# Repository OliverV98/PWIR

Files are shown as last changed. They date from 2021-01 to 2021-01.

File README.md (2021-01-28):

# PWIR

## PINOUT ON STM32CUBEIDE

You can find out more information in PCB schematics or from mainboard V2.ioc

```bash
PF1 - GPIO-I ENC3A - Encoder Motor 3 encoder A
PA0 - GPIO-I ENC2_A - Encoder Motor 2 encoder A
PA2 - GPIO-I ENC1A - Encoder Motor 1 encoder A
PA3 - GPIO-I ENC1B - Encoder Motor 1 encoder B
PA4 - GPIO-I ENC3B - Encoder Motor 3 encoder B
PA5 - GPIO-O ESCPWM 
PA15 - GPIO-O SERVOPWM
PA6 - M1-PWM1 - Mootor 1 PWM1
PA7 - M1-PWM2 - Mootor 1 PWM2
PA8 - M2-PWM1 - Mootor 2 PWM1
PA9 - M2-PWM2 - Mootor 2 PWM2
PB6 - M3-PWM1 - Mootor 3 PWM1
PB7 - M3-PWM2 - Mootor 3 PWM2
PA11 - USB_DM
PA12 - USB_DP
PA13 - SWDIO
PA14 - SWCLK
```

## Functionality of motor drivers

```bash
You get information about the postion of the motor only from one encoder. That is done via GPIO-I(look pinout above). That that is used in the mainboard code to calculate PID and set the motor speed accordingly. Motor drivers get their initial PWM from mainboard that are digitally isolated(really intersting how its done).
```

## Functionality of mainboard
```bash
You send the information from the computer via USB and setup the mainboard using SWDIO and SWCLK. That is done using ST-LINK(ask instructors for it). Mainboard sends out sends out in total 8PWM signals (that of 6 are in pairs for motor drivers,1ESC,1 for servo). Becouse TIMERS were not set up correctly we had to use GIPO-O to generate the PWM signals neccesary for the functionality of ESC and SERVO. Also for the same reasons GIPO-I were used for encoder reading.
```
2021 DELTAX

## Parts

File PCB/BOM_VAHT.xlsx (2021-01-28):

Comment | Description | Designator | Footprint | LibRef | Quantity | Lehekülg | Farnell teko | Mouser teko
KEMET T491B105K035AT | 1uF Solid MnO2 Tantalum Electrolytic Capacitor; 35 V dc +/-10%; T491 Series | C5, C6 | PCB-rufcymyklsjsmb7phwvw-1 | CMP-adcf64c4c6c97208-1 | 2 | https://ee.farnell.com/kemet/t491b105k035at/cap-1-f-35v-10-smd/dp/1457432?CMP=GRHB-OCTOPART | 1457432
Panasonic EEU-FM1E471L | Capacitor; Aluminum Electrolytic; Cap 470uF; Tol 20%; Vol-Rtg 25 VDC; Radial | C9, C18, C21 | Capacitor | CMP-6b23a0732647b4e4-2 | 3 | https://ee.farnell.com/panasonic/eeufm1e471l/cap-470-f-25v-20/dp/1219470?st=panasonic%20eeu-fm1e471l | 1219470
FCI 10118192-0001LF | Conn Micro USB RCP 5 POS 0.65mm Solder RA SMD 5 Terminal 1 Port Embossed T/R | J1 | PCB-y6z8giaxv9oe4jobifng-1 | CMP-5fe6964cc67c8021-5 | 1 | https://ee.farnell.com/amphenol-icc-fci/10118192-0001lf/micro-usb-2-0-type-b-rcpt-smt/dp/2751674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 | 2751674
Bourns SRP5030T-5R6M | Inductor Power Shielded/Molded Wirewound 5.6uH 20% 100KHz Powdered Iron 4.25A 63mOhm DCR T/R | L1 | PCB-hdjvyscrw6xn5uzu8eff-1 | CMP-6d6ca5f0d7c8b2ab-1 | 1 | https://ee.farnell.com/bourns/srp5030t-5r6m/inductor-5-6uh-20-4-25a-power/dp/2309888?st=bourns%20srp5030t-5r6m | 2309888
TE Connectivity / AMP 215079-4 | Conn FFC Connector F 4 POS 1.27mm Solder ST Thru-Hole Automotive Reel | P1, P3, P4, P5, P6 | PCB-rkob87su0l0zzh8rvuwa-1 | CMP-6d83a490a6f7b244-3 | 5 | https://ee.farnell.com/amp-te-connectivity/215079-4/connector-4way-vertical-1-27/dp/1772996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 | 1772996
Samtec FTSH-105-01-L-D | CLEAR GLOVE BX 100 M - More Details | P2 | PINHEAD_2X05_127 | CMP-667845-3 | 1 | https://ee.farnell.com/samtec/ftsh-105-01-l-d/connector-header-1-27mm-pcb-10way/dp/2308436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 | 2308436
ON Semiconductor FDD6685 | MOSFET Transistor, P Channel, -40 A, -30 V, 0.014 ohm, -10 V, -1.8 V | Q1 | INF-PG-TO252-3-11_M | CMP-1302df0e83a1ccc5-2 | 1 | https://ee.farnell.com/on-semiconductor/fdd6685/mosfet-p-smd-to-252/dp/1471043?st=on%20semiconductor%20fdd6685 | 1471043
LM2937IMP-5.0/NOPB | 500 mA Low Dropout Regulator, 4-pin SOT-223, Pb-Free | U1 | MP04A_L | CMP-0062-01757-3 | 1 | https://ee.farnell.com/texas-instruments/lm2937imp-5-0-nopb/ldo-0-5vdo-5v-0-5a-3sot223/dp/3122066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 | 3122066
STMicroelectronics USBLC6-2SC6 | USBLC6 Series 2 Line 6 V Uni / Bi-Directional ESD Protection - SOT-23-6 | U2 | SOT95P280X145-6N | CMP-756ebe39126caaa9-8 | 1 | https://ee.farnell.com/stmicroelectronics/usblc6-2sc6/esd-protection-3-5pf-17v-sot23/dp/1269406RL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 | 1269406RL
Texas Instruments ISO7760DWR | High Speed, Robust EMC Six-Channel Digital Isolators 16-SOIC -55 to 125 | U3 | PCB-tizc0j283js4s37wua64-1 | CMP-7f8db395d75da04a-1 | 1 | https://www.mouser.ee/ProductDetail/Texas-Instruments/ISO7760DWR?qs=BZBei1rCqCAKosCUp1v8Jg%3D%3D |  | 595- ISO7760DWR
MCP1701AT-3302I/CB | 2 µA Low-Dropout Positive Voltage Regulator, 3-Pin SOT-23A, Industrial Temperature, Tape and Reel | U4 | SOT-23A-CB3_L | CMP-1501331-2 | 1 | https://ee.farnell.com/microchip/mcp1701at-3302i-cb/ic-ldo-reg-250ma-3-3v-sot-23a/dp/1605554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 | 1605554
STMicroelectronics STM32G431K8T6 | Mainstream Arm CORTEX-M4 Core Wi | U5 | PCB-roa9pse9auixlf5bq7cm-1 | CMP-333afc1f6528ecfd-2 | 1 | https://ee.farnell.com/stmicroelectronics/stm32g431k8t6/mcu-32bit-170mhz-lqfp-32/dp/3515807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 | 3515807
Texas Instruments DRV8874PWPR | 38-V, 6-A H-bridge motor driver with integrated current sensing & feedback 16-HTSSOP -40 to 125 | U6, U7, U8 | PCB-45171vetpwtrcknlr443-1 | CMP-1fd4d0c2f6c9c013-7 | 3 | https://www.mouser.ee/ProductDetail/Texas-Instruments/DRV8874PWPR |  | 595-DRV8874PWPR
SI8620BB-B-IS | General Purpose tal Isolator 2500Vrms 2 Channel 150Mbps 35kV/µs CMTI 8-SOIC (0.154 , 3.90mm Width) | U9 | PCB-426hnsna86ae4ms1a3g5-1 | CMP-11cfd913bf49ce08-1 | 1 | https://ee.farnell.com/silicon-labs/si8620bb-b-is/digital-isolator-8ns-nsoic-8/dp/2423240?CMP=GRHB-OCTOPART | 2423240
Texas Instruments TPS56339DDCR | 4.5-V to 24-V input, 3-A output synchronous buck converter 6-SOT-23-THIN -40 to 125 | U10 | PCB-gq8lm18lv5jhlhr4rj8l-1 | CMP-bcda73dcd896631d-3 | 1 | https://www.mouser.ee/ProductDetail/Texas-Instruments/TPS56339DDCR |  | 595-TPS56339DDCR
teko = | tellimiskood

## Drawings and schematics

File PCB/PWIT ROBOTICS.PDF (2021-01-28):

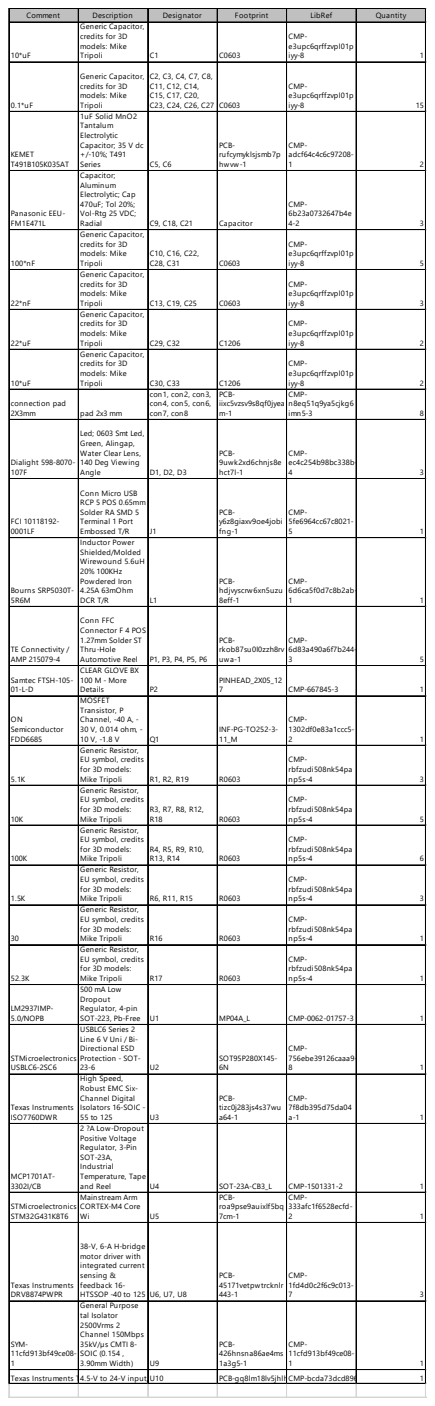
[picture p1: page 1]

Comment | Description | Designator | Footprint | LibRef | Quantity
10*uF | Generic Capacitor, credits for 3D models: Mike Tripoli | C1 | C0603 | CMP-e3upc6qrffzvpl01p iyy-8 | 1

0.1*uF | Generic Capacitor, credits for 3D models: Mike Tripoli | C2, C3, C4, C7, C8, C11, C12, C14, C15, C17, C20, C23, C24, C26, C27 | C0603 | CMP-e3upc6qrffzvpl01p iyy-8 | 15

KEMET T491B105K035AT | 1uF Solid MnO2 Tantalum Electrolytic Capacitor; 35 V dc +/-10%; T491 Series | C5, C6 | PCB-rufcymyklsjsmb7p hwvw-1 | CMP-adcf64c4c6c97208-1 | 2

Panasonic EEU-FM1E471L | Capacitor; Aluminum Electrolytic; Cap 470uF; Tol 20%; Vol-Rtg 25 VDC; Radial | C9, C18, C21 | Capacitor | CMP-6b23a0732647b4e 4-2 | 3

100*nF | Generic Capacitor, credits for 3D models: Mike Tripoli | C10, C16, C22, C28, C31 | C0603 | CMP-e3upc6qrffzvpl01p iyy-8 | 5

22*nF | Generic Capacitor, credits for 3D models: Mike Tripoli | C13, C19, C25 | C0603 | CMP-e3upc6qrffzvpl01p iyy-8 | 3

22*uF | Generic Capacitor, credits for 3D models: Mike Tripoli | C29, C32 | C1206 | CMP-e3upc6qrffzvpl01p iyy-8 | 2

10*uF | Generic Capacitor, credits for 3D models: Mike Tripoli | C30, C33 | C1206 | CMP-e3upc6qrffzvpl01p iyy-8 | 2

connection pad 2X3mm | pad 2x3 mm | con1, con2, con3, con4, con5, con6, con7, con8 | PCB-iixc5vzsv9s8qf0jyea m-1 | CMP-n8eq51q9ya5cjkg6 imn5-3 | 8

Dialight 598-8070-107F | Led; 0603 Smt Led, Green, Alingap, Water Clear Lens, 140 Deg Viewing Angle | D1, D2, D3 | PCB-9uwk2xd6chnjs8e hct7l-1 | CMP-ec4c254b98bc338b-4 | 3

FCI 10118192-0001LF | Conn Micro USB RCP 5 POS 0.65mm Solder RA SMD 5 Terminal 1 Port Embossed T/R | J1 | PCB-y6z8giaxv9oe4jobi fng-1 | CMP-5fe6964cc67c8021-5 | 1

Bourns SRP5030T-5R6M | Inductor Power Shielded/Molded Wirewound 5.6uH 20% 100KHz Powdered Iron 4.25A 63mOhm DCR T/R | L1 | PCB-hdjvyscrw6xn5uzu 8eff-1 | CMP-6d6ca5f0d7c8b2ab-1 | 1

TE Connectivity / AMP 215079-4 | Conn FFC Connector F 4 POS 1.27mm Solder ST Thru-Hole Automotive Reel | P1, P3, P4, P5, P6 | PCB-rkob87su0l0zzh8rv uwa-1 | CMP-6d83a490a6f7b244-3 | 5

Samtec FTSH-105-01-L-D | CLEAR GLOVE BX 100 M - More Details | P2 | PINHEAD_2X05_12 7 | CMP-667845-3 | 1

ON Semiconductor FDD6685 | MOSFET Transistor, P Channel, -40 A, -30 V, 0.014 ohm, -10 V, -1.8 V | Q1 | INF-PG-TO252-3-11_M | CMP-1302df0e83a1ccc5-2 | 1

5.1K | Generic Resistor, EU symbol, credits for 3D models: Mike Tripoli | R1, R2, R19 | R0603 | CMP-rbfzudi508nk54pa np5s-4 | 3

10K | Generic Resistor, EU symbol, credits for 3D models: Mike Tripoli | R3, R7, R8, R12, R18 | R0603 | CMP-rbfzudi508nk54pa np5s-4 | 5

100K | Generic Resistor, EU symbol, credits for 3D models: Mike Tripoli | R4, R5, R9, R10, R13, R14 | R0603 | CMP-rbfzudi508nk54pa np5s-4 | 6

1.5K | Generic Resistor, EU symbol, credits for 3D models: Mike Tripoli | R6, R11, R15 | R0603 | CMP-rbfzudi508nk54pa np5s-4 | 3

30 | Generic Resistor, EU symbol, credits for 3D models: Mike Tripoli | R16 | R0603 | CMP-rbfzudi508nk54pa np5s-4 | 1

52.3K | Generic Resistor, EU symbol, credits for 3D models: Mike Tripoli | R17 | R0603 | CMP-rbfzudi508nk54pa np5s-4 | 1

LM2937IMP-5.0/NOPB | 500 mA Low Dropout Regulator, 4-pin SOT-223, Pb-Free | U1 | MP04A_L | CMP-0062-01757-3 | 1

STMicroelectronics USBLC6-2SC6 | USBLC6 Series 2 Line 6 V Uni / Bi-Directional ESD Protection - SOT-23-6 | U2 | SOT95P280X145-6N | CMP-756ebe39126caaa9-8 | 1

Texas Instruments ISO7760DWR | High Speed, Robust EMC Six-Channel Digital Isolators 16-SOIC -55 to 125 | U3 | PCB-tizc0j283js4s37wu a64-1 | CMP-7f8db395d75da04 a-1 | 1

MCP1701AT-3302I/CB | 2 ?A Low-Dropout Positive Voltage Regulator, 3-Pin SOT-23A, Industrial Temperature, Tape and Reel | U4 | SOT-23A-CB3_L | CMP-1501331-2 | 1

STMicroelectronics STM32G431K8T6 | Mainstream Arm CORTEX-M4 Core Wi | U5 | PCB-roa9pse9auixlf5bq 7cm-1 | CMP-333afc1f6528ecfd-2 | 1

Texas Instruments DRV8874PWPR | 38-V, 6-A H-bridge motor driver with integrated current sensing & feedback 16-HTSSOP -40 to 125 | U6, U7, U8 | PCB-45171vetpwtrcknlr 443-1 | CMP-1fd4d0c2f6c9c013-7 | 3

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

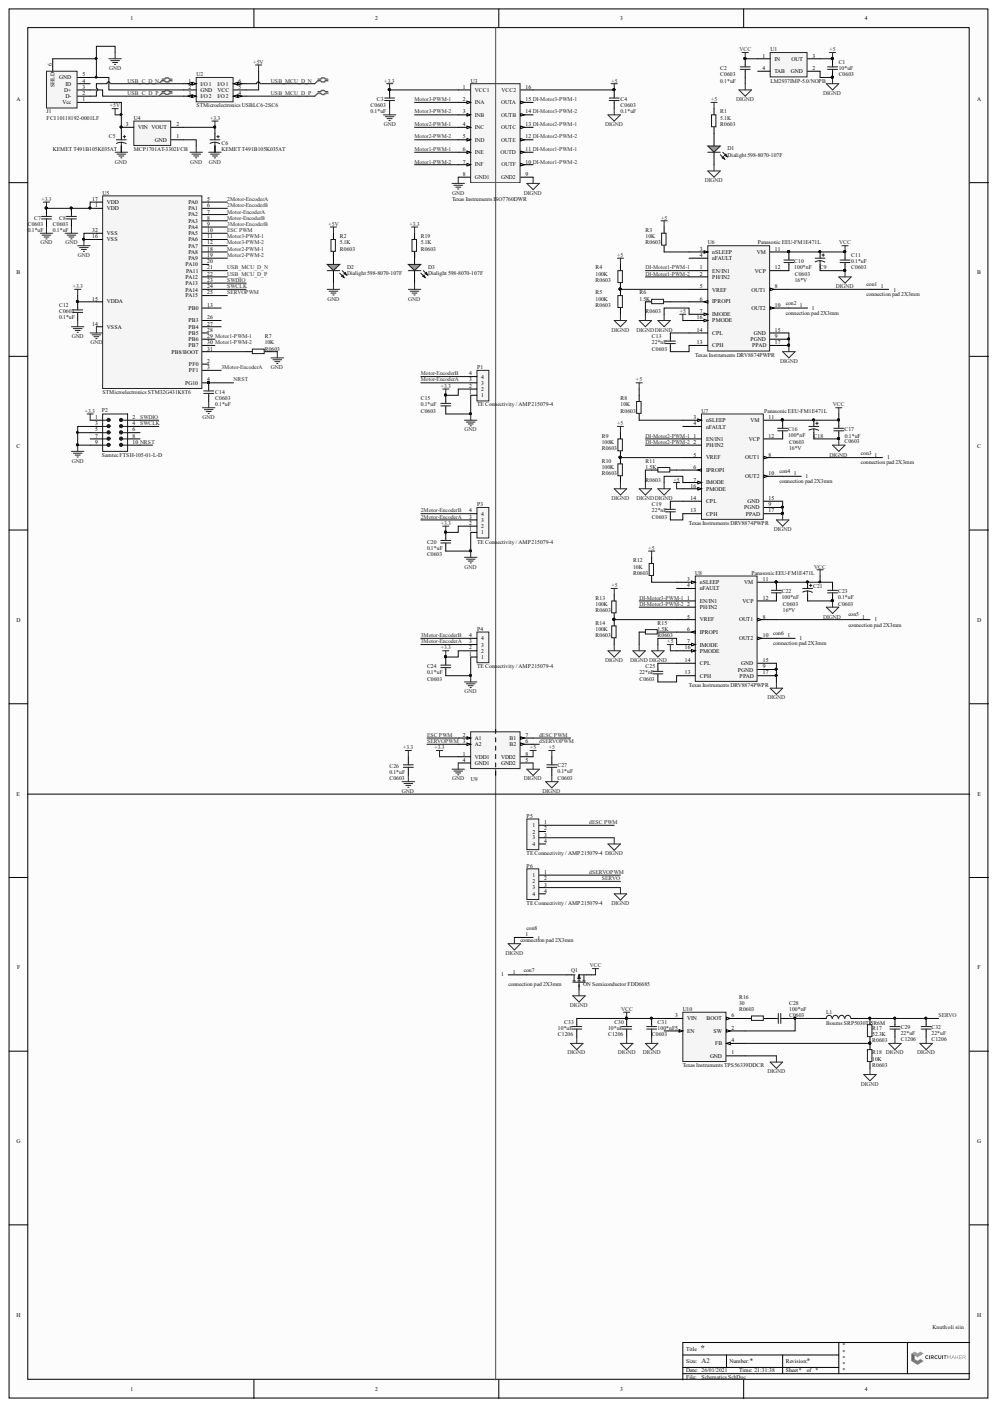
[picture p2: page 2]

VCC U1 +5 +5 R3

Title * | * * * * *

1 2 | 3 | File: Schematics.SchDoc 4

Size: A2 | Number: * | Revision: *

Date: 26/01/2021 Time: 21:31:38 | | Sheet * of *

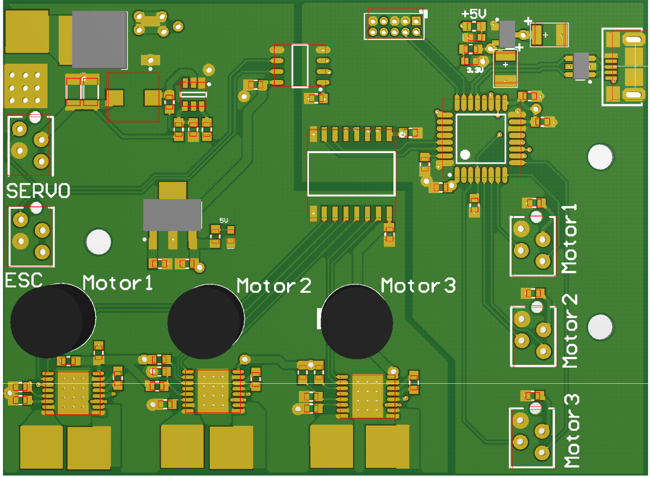
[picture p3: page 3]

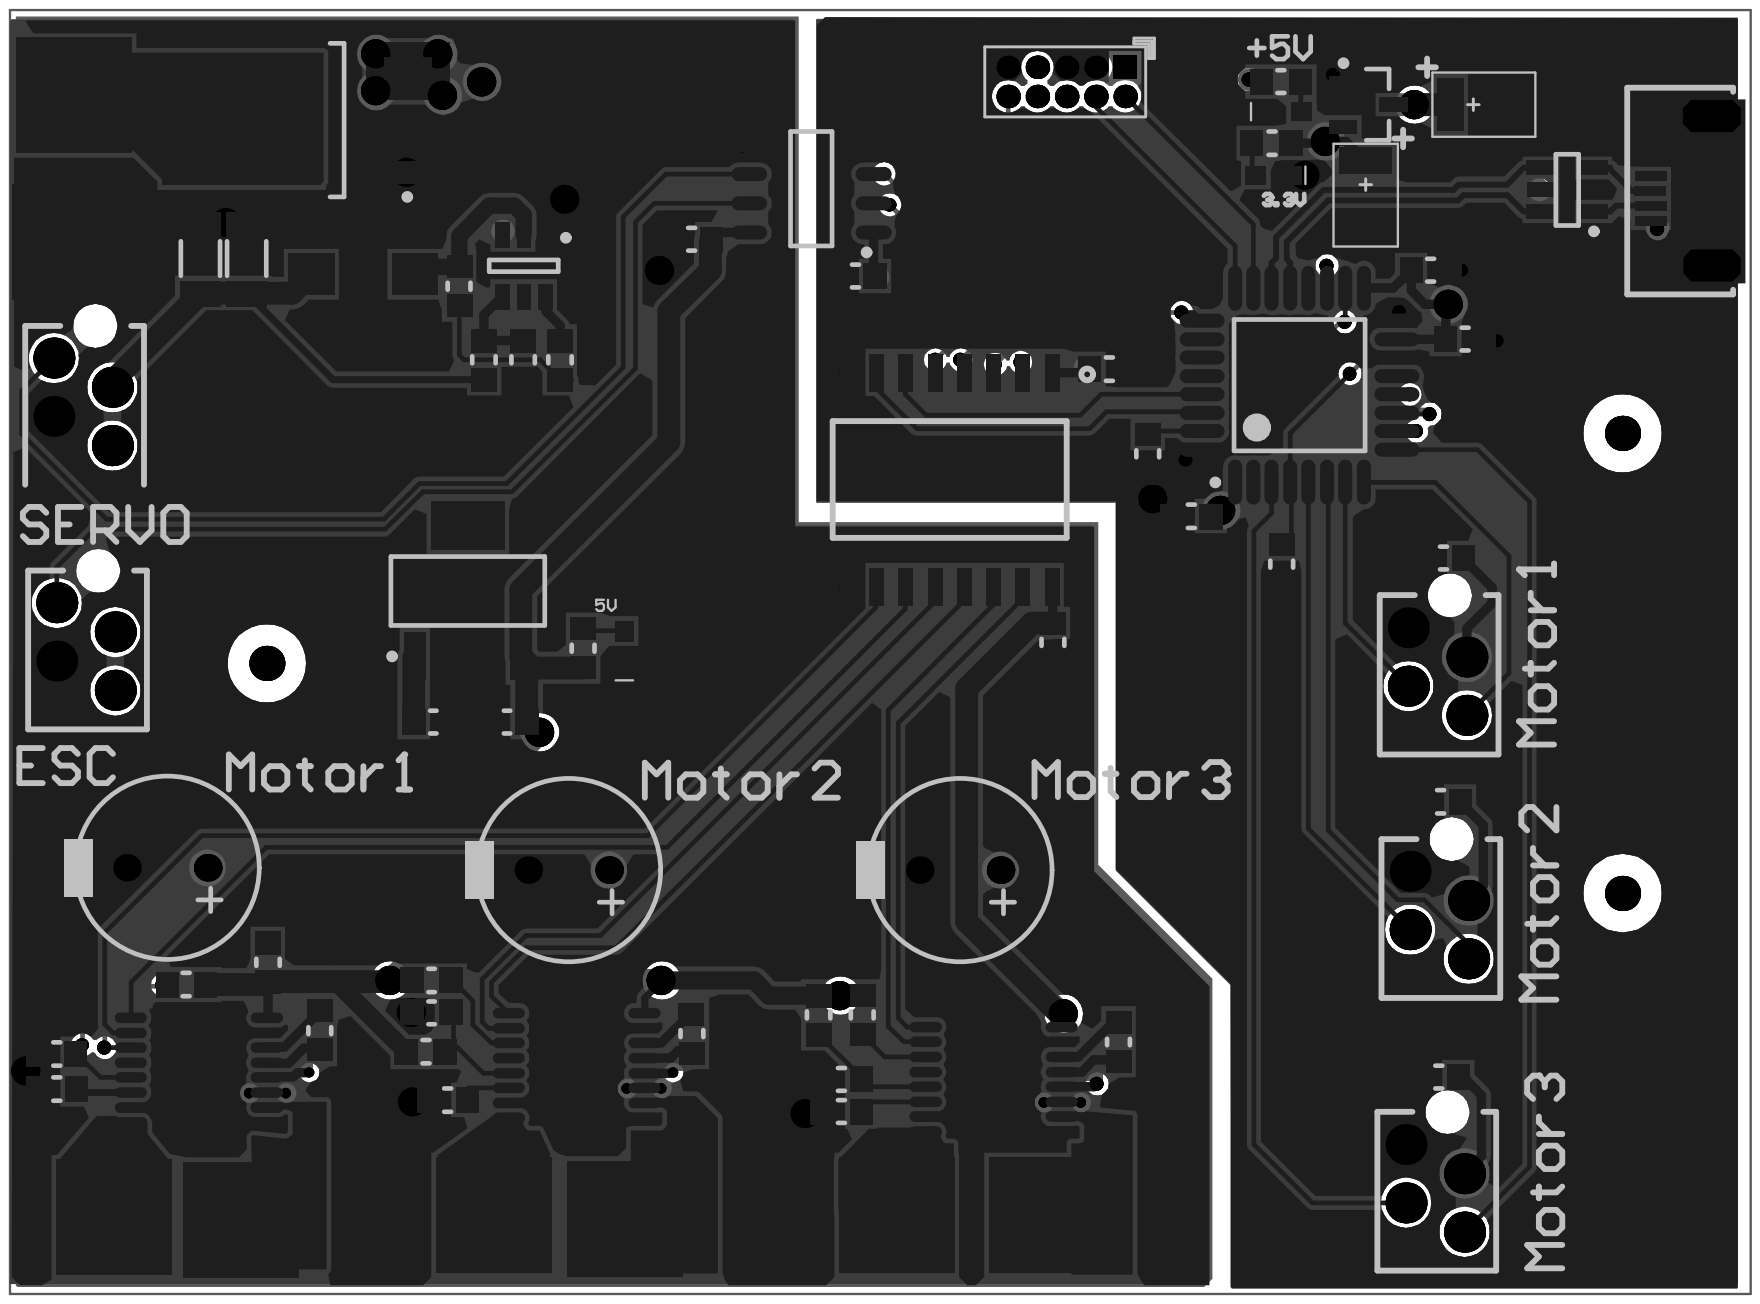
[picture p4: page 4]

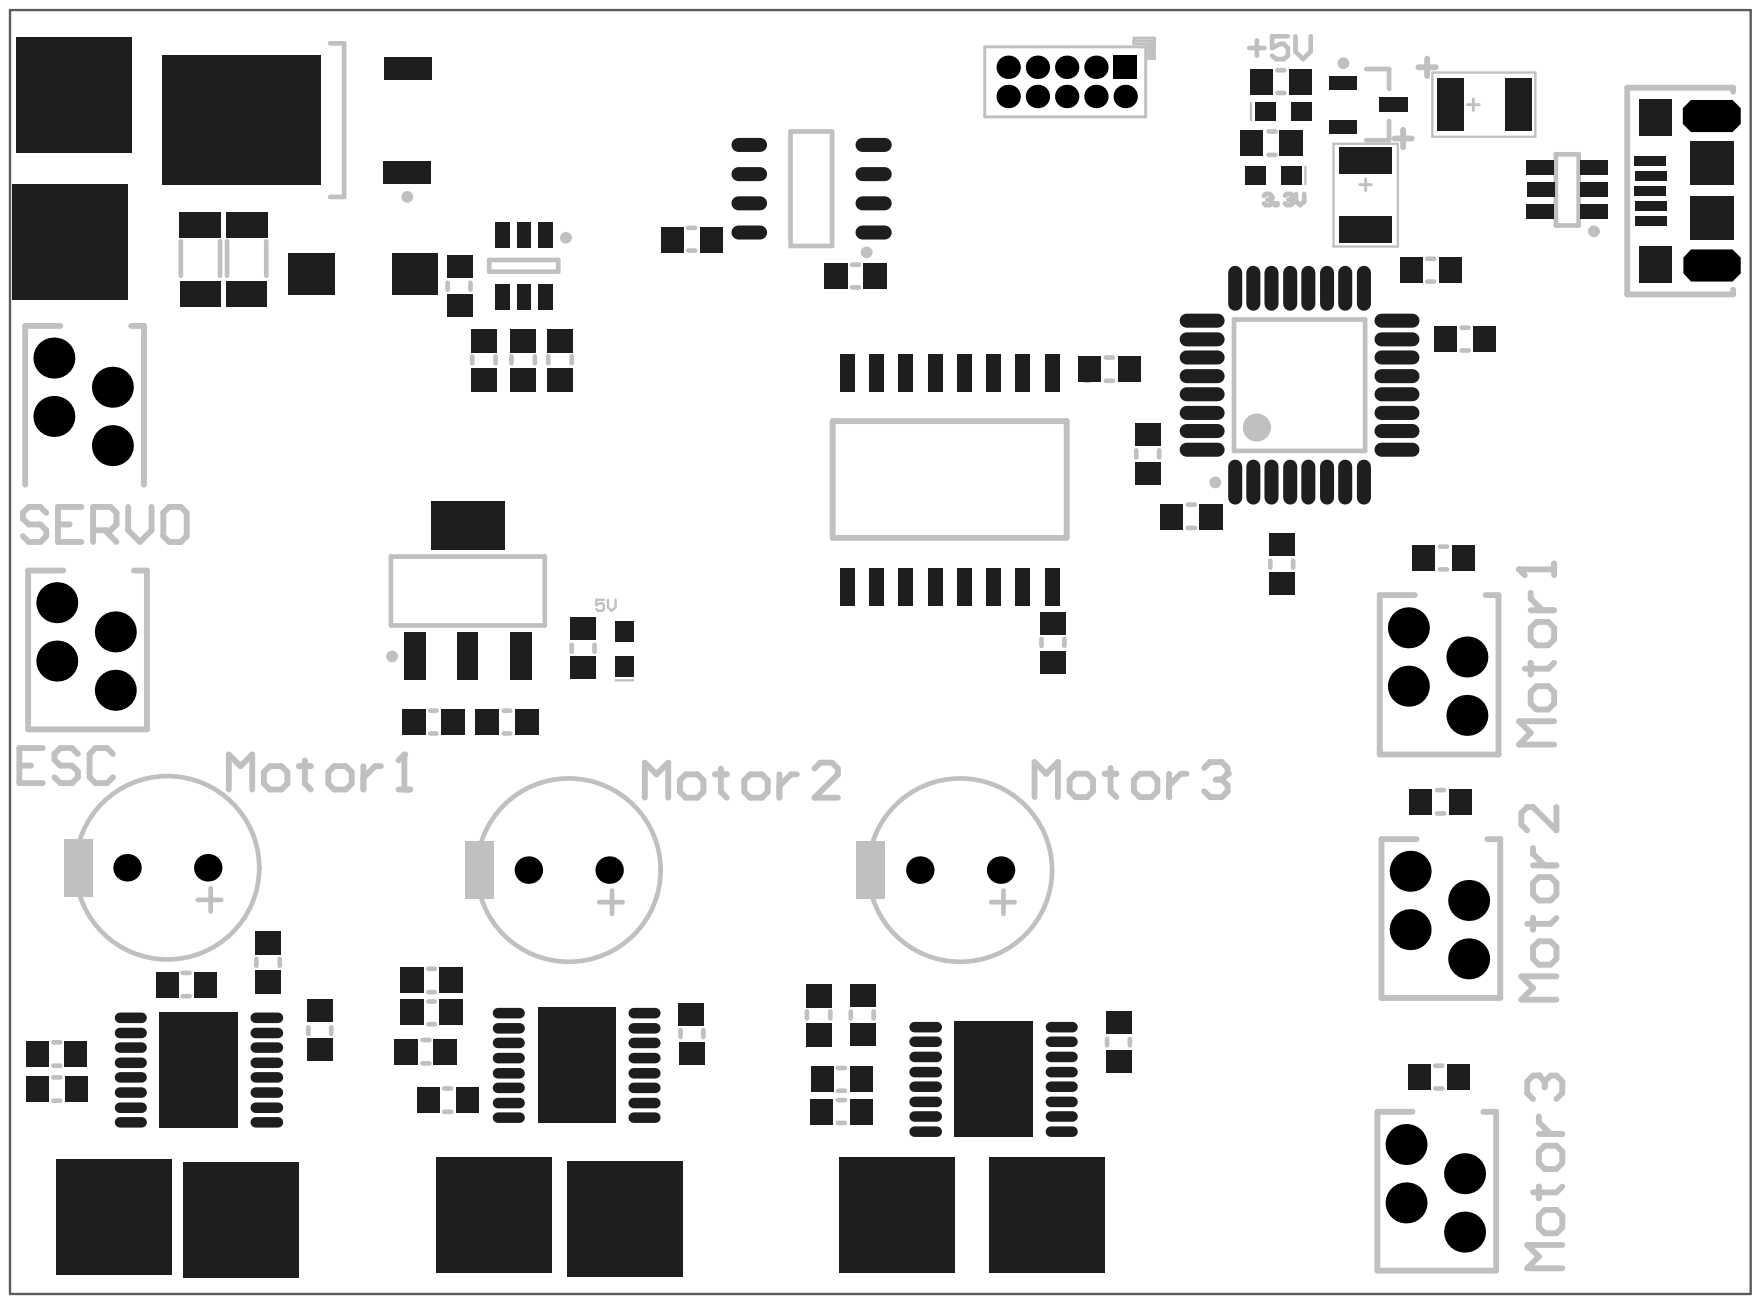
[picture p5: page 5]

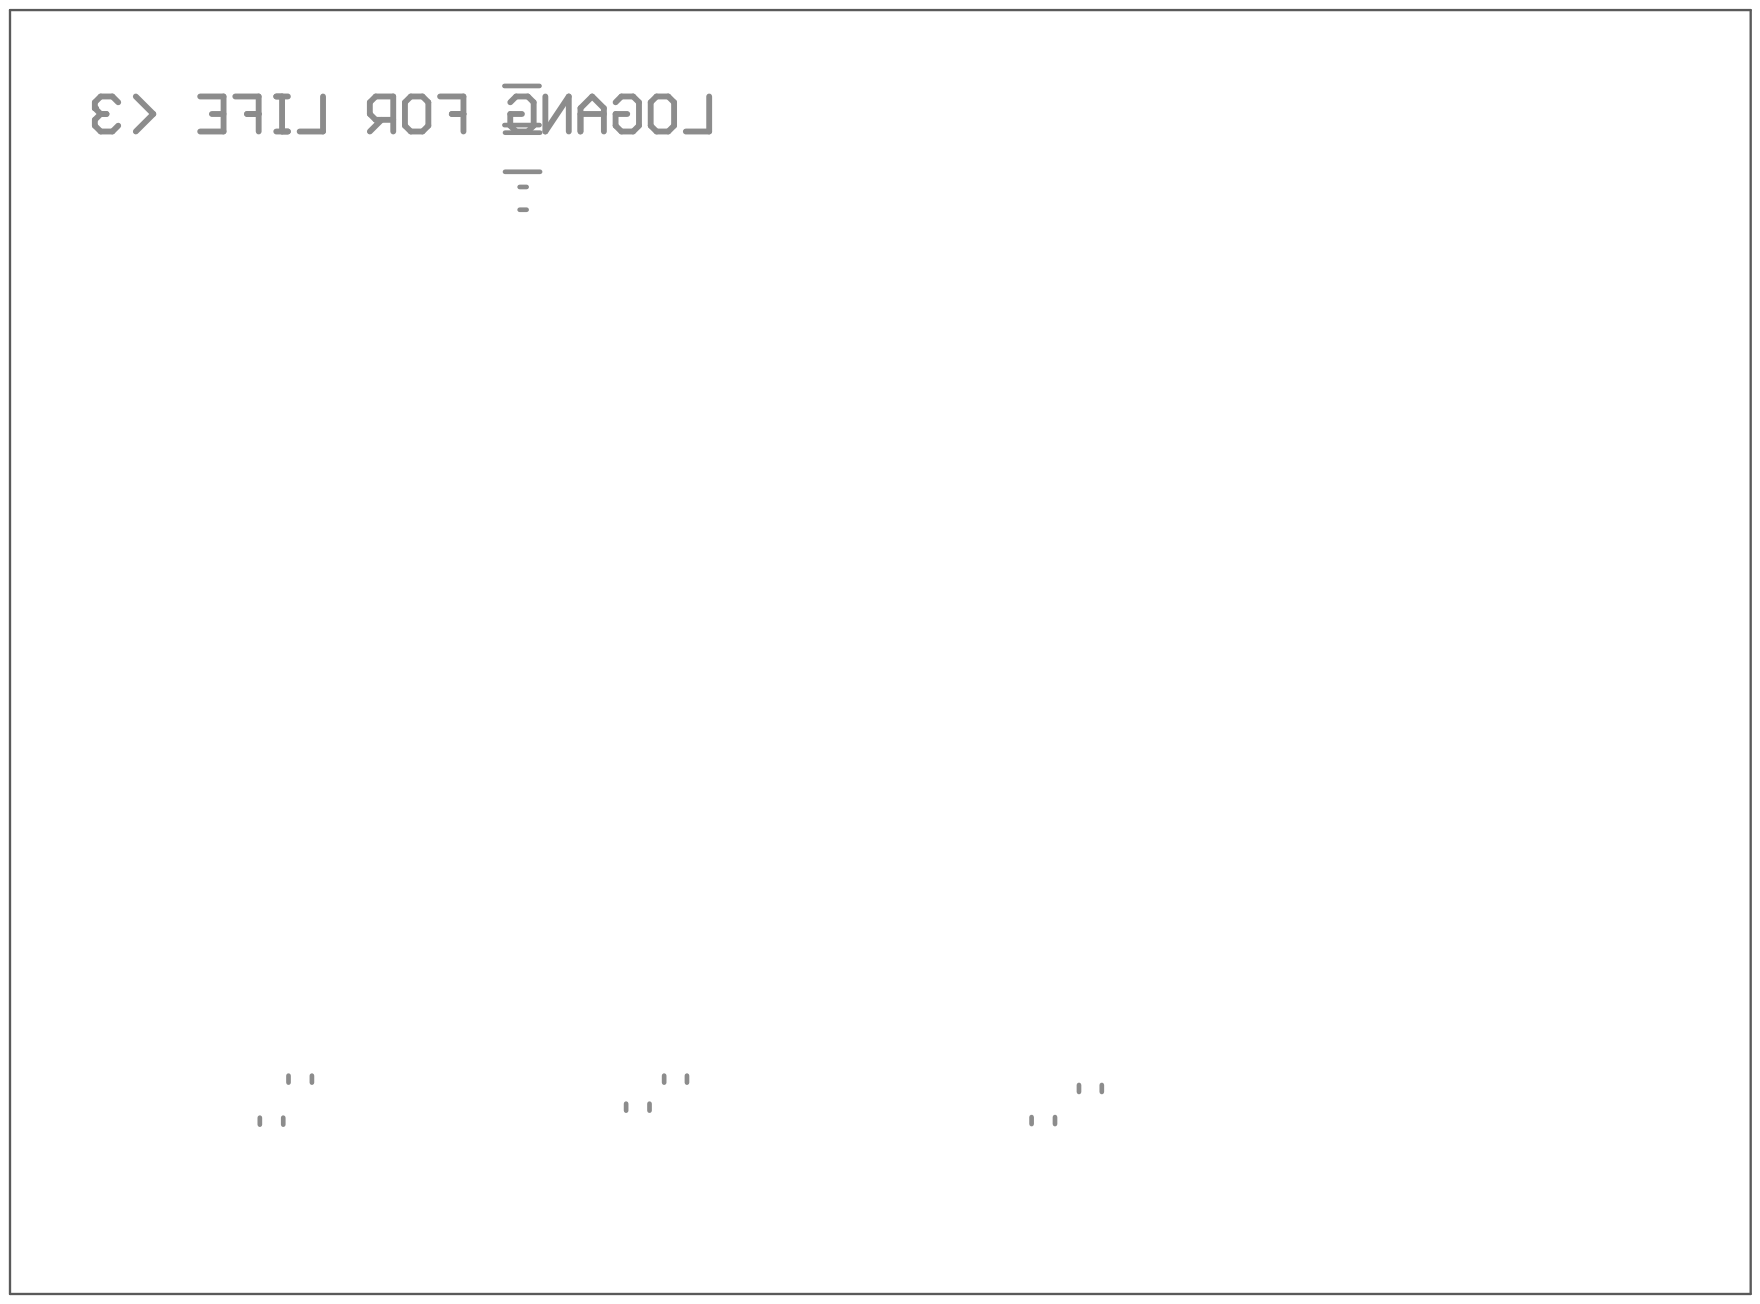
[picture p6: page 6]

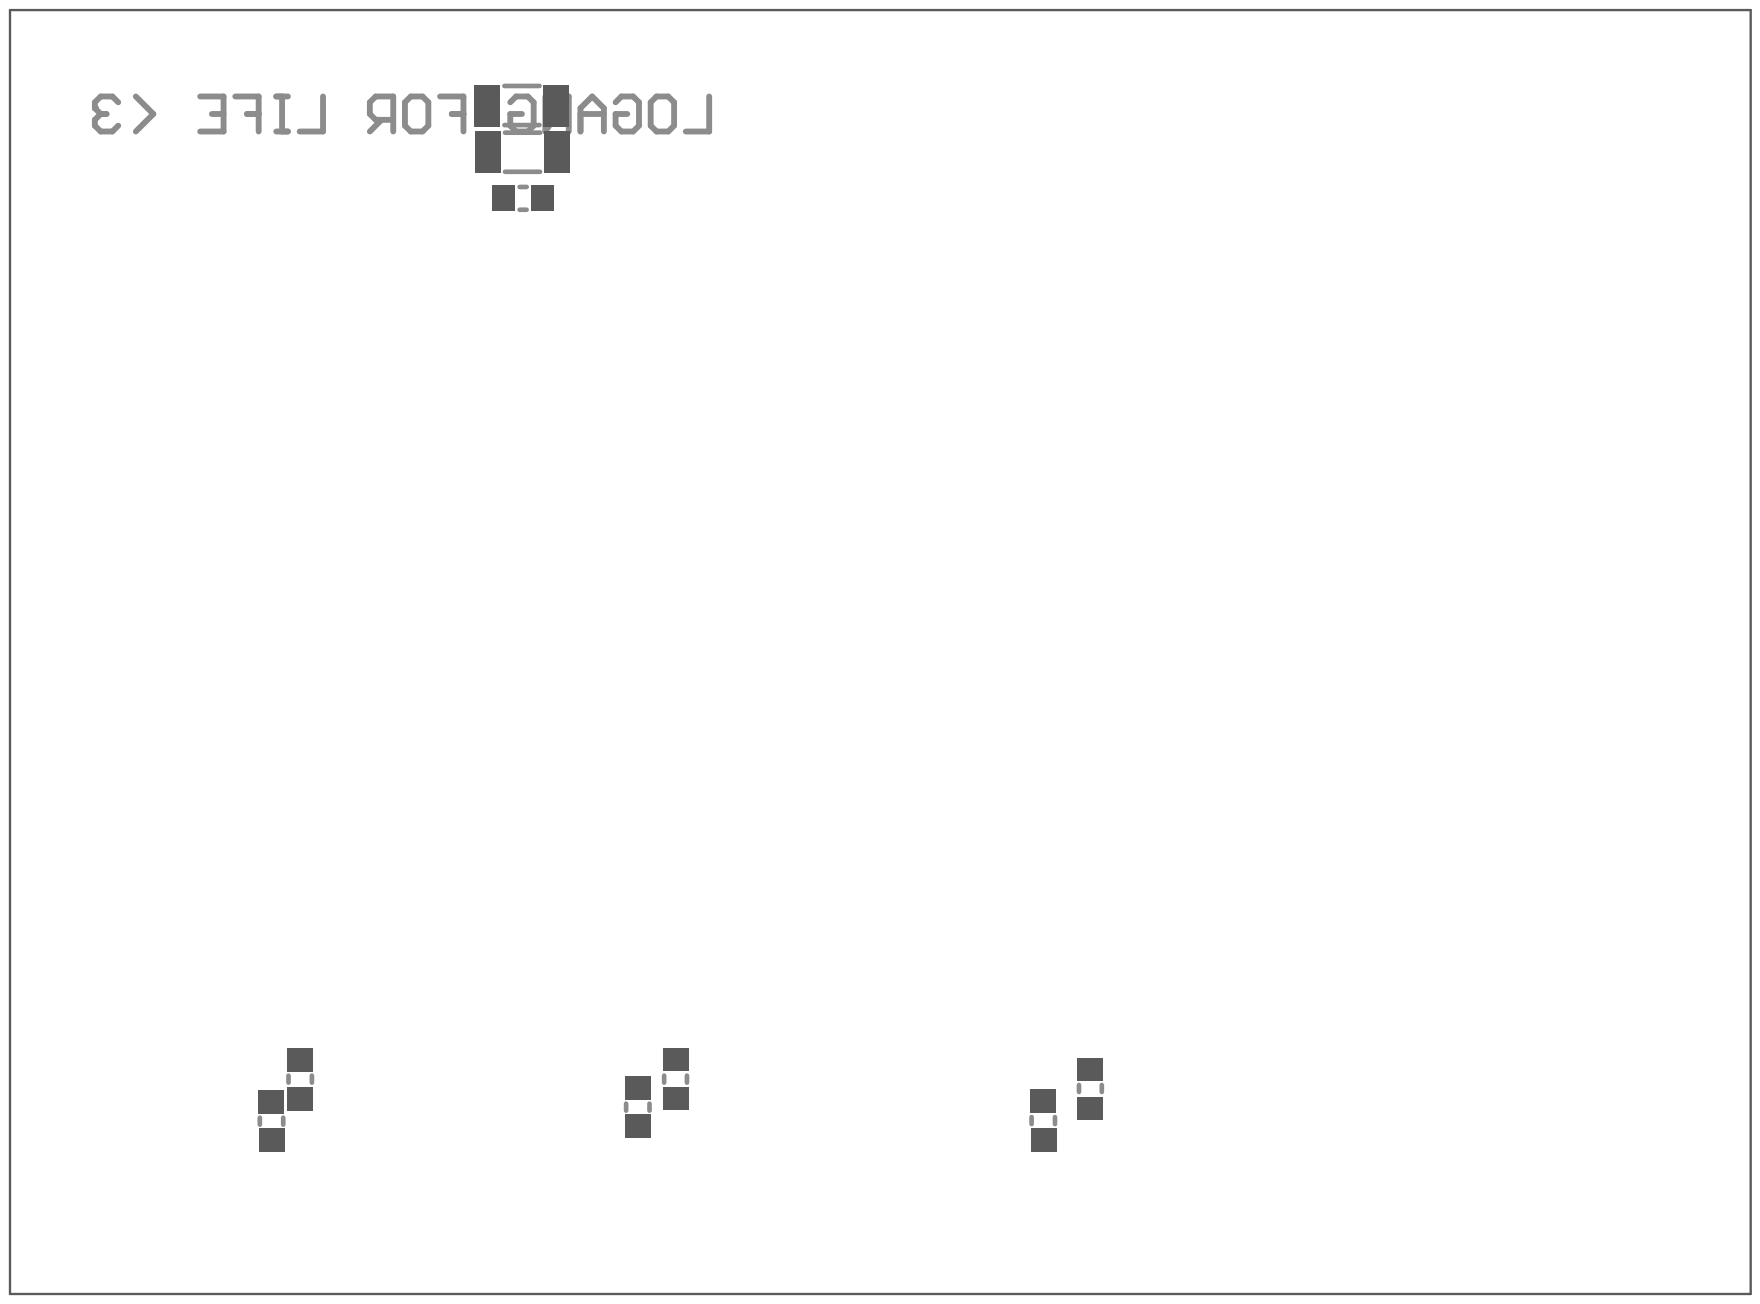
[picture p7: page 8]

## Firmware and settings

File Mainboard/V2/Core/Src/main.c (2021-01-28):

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
/* Includes ------------------------------------------------------------------*/
#include "main.h"
#include "usb_device.h"

TIM_HandleTypeDef htim1;
TIM_HandleTypeDef htim3;
TIM_HandleTypeDef htim4;
TIM_HandleTypeDef htim8;
TIM_HandleTypeDef htim16;

void SystemClock_Config(void);
static void MX_GPIO_Init(void);
static void MX_TIM1_Init(void);
static void MX_TIM3_Init(void);
static void MX_TIM4_Init(void);
static void MX_TIM8_Init(void);
static void MX_TIM16_Init(void);
/* USER CODE BEGIN 0 */
typedef struct Command { // (1)
	int8_t motor1;
	int8_t motor2;
	int8_t motor3;
	int32_t thrower;
	int32_t servo;
	int32_t ir;
//	float pGain;
//	float iGain;
//	float dGain;
	int32_t pid_type;
	uint8_t delimiter;
	int8_t speed1;
	int8_t speed2;
	int8_t speed3;
	int8_t throwerSpeed;

} Command;


Command command, feedback;
volatile uint8_t command_received = 0;
volatile uint8_t command_received_ticker = 0;

Motor motor1;
Motor motor2;
Motor motor3;


typedef struct Feedback { // (3)
  int16_t speed1;
  int16_t speed2;
  int16_t speed3;
  uint16_t delimiter;
} Feedback;

typedef struct Received{
	uint8_t speed1;
	uint8_t speed2;
	uint8_t speed3;
	uint8_t throwerSpeed;
	uint8_t servospeed;
	uint8_t delimiter;
} Received;

Received received = {.speed1 = 125, .speed2 = 125, .speed3 = 125, .throwerSpeed = 0,.servospeed = 0, .delimiter = 0}; // (4)
volatile uint8_t isCommandReceived = 0; // (5)
volatile float pGain, iGain, dGain = 0;


void CDC_On_Receive(uint8_t* buffer, uint32_t* length) {

  if (*length == sizeof(Received)) {
	  memcpy(&received, buffer, sizeof(Received));

	 if (received.delimiter == 0xAA) { // (9)
		  isCommandReceived = 1;
    }
  }
}


void Set_Motor_Speed(volatile uint32_t *channel_a, //copy paste
		volatile uint32_t *channel_b, int32_t motor_speed) {
	if (motor_speed > 0) {
		// forward
		if (motor_speed <= MOTORS_MAX_SPEED) {
			// 0 to 100 compact range
			*channel_a = motor_speed * MOTORS_CO + MOTORS_MIN_CCR;
		} else {
			// 100 to 65535 full range
			*channel_a = motor_speed;
		}
		*channel_b = 0;
	} else if (motor_speed < 0) {
		// backward
		if (motor_speed >= -MOTORS_MAX_SPEED) {
			// -100 to 0 compact range
			*channel_b = motor_speed * -MOTORS_CO + MOTORS_MIN_CCR;
		} else {
			// -65535 to -100 full range
			*channel_b = motor_speed * -1;
		}
		*channel_a = 0;
	} else {
		// stop
		*channel_a = 0;
		*channel_b = 0;
	}
}


int PID2(uint8_t enc, uint8_t setpoint){


	enc = 250 - enc;

	float P = 0.4;
	float I = 0.00001;
	float D = 0;

	static long integral = 0;

	if(setpoint == 0){
		integral = 0;
		return 0;
	}


	//CDC_Transmit_FS(&enc, sizeof(enc));

	float error = setpoint - enc;

	integral += error;

	int out = 50 + P*error + I*integral;

	if(out < 0){
		out = 0;
	}


	if(out > 100) out = 100;

	//CDC_Transmit_FS(&out, sizeof(out));
	return (uint8_t)out;
}
/* USER CODE END 0 */

/**
  * @brief  The application entry point.
  * @retval int
  */
int main(void)
{
  /* USER CODE BEGIN 1 */


    /* Initialize Rotary encoder 2, pin A = PF1, pin B = PA2 */


    /* Rotate LCD */

    /* Initialize Rotary encoder 1, pin A = PF1, pin B = PD1 */

  /* USER CODE END 1 */

  /* MCU Configuration--------------------------------------------------------*/

  /* Reset of all peripherals, Initializes the Flash interface and the Systick. */
  HAL_Init();

  /* USER CODE BEGIN Init */
  CoreDebug->DEMCR |= CoreDebug_DEMCR_TRCENA_Msk;
    DWT->CYCCNT = 0;
    DWT->CTRL |= DWT_CTRL_CYCCNTENA_Msk;

    unsigned long esctimer = DWT->CYCCNT;
    unsigned long servotimer = DWT->CYCCNT;
  /* USER CODE END Init */

  /* Configure the system clock */
  SystemClock_Config();

  /* Initialize all configured peripherals */
  MX_GPIO_Init();
  MX_TIM1_Init();
  MX_TIM3_Init();
  MX_TIM4_Init();
  MX_TIM8_Init();
  MX_TIM16_Init();
  MX_USB_Device_Init();
  /* USER CODE BEGIN 2 */
 // HAL_TIM_Encoder_Start(&htim2, TIM_CHANNEL_1 | TIM_CHANNEL_2);

    HAL_TIM_PWM_Start(&htim1, TIM_CHANNEL_1);
  	HAL_TIM_PWM_Start(&htim1, TIM_CHANNEL_2);
  	TIM1->CCR1 = 0;
  	TIM1->CCR2 = 0;


  	HAL_TIM_PWM_Start(&htim3, TIM_CHANNEL_1);
  	HAL_TIM_PWM_Start(&htim3, TIM_CHANNEL_2);
  	TIM3->CCR1 = 0;
  	TIM3->CCR2 = 0;


  	HAL_TIM_PWM_Start(&htim4, TIM_CHANNEL_1);
  	HAL_TIM_PWM_Start(&htim4, TIM_CHANNEL_2);
  	TIM4->CCR1 = 0;
  	TIM4->CCR2 = 0;


typedef struct Feedback{
	int16_t speed1;
	int16_t speed2;
	int16_t speed3;
	int16_t delmiter;
} Feedback;

  /* USER CODE END 2 */

  /* Infinite loop */
  /* USER CODE BEGIN WHILE */
	int ENC2 = 0;
	int prev_ENC2 = 0;
	unsigned long ENCA_S = DWT->CYCCNT;
	unsigned long ENCA_D;
	uint8_t ENCA_P = 0;

	unsigned long ENCA_S1 = DWT->CYCCNT;
	unsigned long ENCA_D1;
	uint8_t ENCA_P3 = 0;

	unsigned long ENCA_S3 = DWT->CYCCNT;
	unsigned long ENCA_D3;
	uint8_t ENCA_P2 = 0;
  while (1)
  {


	  //ESC
	  if((DWT->CYCCNT - esctimer)/96000 > 20){
		  esctimer = DWT->CYCCNT;
		  HAL_GPIO_WritePin(ESCPWM_GPIO_Port, ESCPWM_Pin,1);
		  while((DWT->CYCCNT - esctimer) / 96 < (received.throwerSpeed*3.92+1000));
		  HAL_GPIO_WritePin(ESCPWM_GPIO_Port, ESCPWM_Pin,0);
	  }



	  //SERVO
	  if((DWT->CYCCNT - servotimer)/96000 > 2){
		  servotimer = DWT->CYCCNT;
		  HAL_GPIO_WritePin(SERVOPWM_GPIO_Port, SERVOPWM_Pin,1);
		  while((DWT->CYCCNT - servotimer) / 96 < (received.servospeed*23));
		  HAL_GPIO_WritePin(SERVOPWM_GPIO_Port, SERVOPWM_Pin,0);
	  }







	  	  unsigned long while_timeout = DWT->CYCCNT;
	  	  int timeout_flag = 0;
		  while(HAL_GPIO_ReadPin(ENC2_A_GPIO_Port, ENC2_A_Pin) == 1){  // ootab kuni läheb madalaks
			  if((DWT->CYCCNT - while_timeout)/2000 > 249){
				  timeout_flag = 1;
				  break;
			  }
		  }
		  while_timeout = DWT->CYCCNT;
		  while(HAL_GPIO_ReadPin(ENC2_A_GPIO_Port, ENC2_A_Pin) == 0){ //ootab kuni läheb kõrgeks
			  if((DWT->CYCCNT - while_timeout)/2000 > 249){
				  timeout_flag = 1;
				  break;
			  }
		  }
		  while_timeout = DWT->CYCCNT;
		  ENCA_S = DWT->CYCCNT;
		  while(HAL_GPIO_ReadPin(ENC2_A_GPIO_Port, ENC2_A_Pin) == 1){ // ootab kuni läheb madalaks
			  if((DWT->CYCCNT - while_timeout)/2000 > 249){
				  timeout_flag = 1;
				  break;
			  }
		  }

		  ENCA_D = ((DWT->CYCCNT - ENCA_S) / 2000);
		  if(ENCA_D > 249 || timeout_flag == 1) ENCA_D = 249;
		  ENCA_P = (uint8_t)ENCA_D;





		  while_timeout = DWT->CYCCNT;
		  timeout_flag = 0;
		  while(HAL_GPIO_ReadPin(ENC1A_GPIO_Port, ENC1A_Pin) == 1){  // ootab kuni läheb madalaks
			  if((DWT->CYCCNT - while_timeout)/2000 > 249){
				  timeout_flag = 1;
				  break;
			  }
		  }
		  while_timeout = DWT->CYCCNT;
		  while(HAL_GPIO_ReadPin(ENC1A_GPIO_Port, ENC1A_Pin) == 0){ //ootab kuni läheb kõrgeks
			  if((DWT->CYCCNT - while_timeout)/2000 > 249){
				  timeout_flag = 1;
				  break;
			  }
		  }
		  while_timeout = DWT->CYCCNT;
		  ENCA_S = DWT->CYCCNT;
		  while(HAL_GPIO_ReadPin(ENC1A_GPIO_Port, ENC1A_Pin) == 1){ // ootab kuni läheb madalaks
			  if((DWT->CYCCNT - while_timeout)/2000 > 249){
				  timeout_flag = 1;
				  break;
			  }
		  }

		  ENCA_D = ((DWT->CYCCNT - ENCA_S) / 2000);
		  if(ENCA_D > 249 || timeout_flag == 1) ENCA_D = 249;
		  ENCA_P3 = (uint8_t)ENCA_D;







		  while_timeout = DWT->CYCCNT;
  	  	  timeout_flag = 0;
  		  while(HAL_GPIO_ReadPin(ENC3A_GPIO_Port, ENC3A_Pin) == 1){  // ootab kuni läheb madalaks
  			  if((DWT->CYCCNT - while_timeout)/2000 > 249){
  				  timeout_flag = 1;
  				  break;
  			  }
  		  }
  		  while_timeout = DWT->CYCCNT;
  		  while(HAL_GPIO_ReadPin(ENC3A_GPIO_Port, ENC3A_Pin) == 0){ //ootab kuni läheb kõrgeks
  			  if((DWT->CYCCNT - while_timeout)/2000 > 249){
  				  timeout_flag = 1;
  				  break;
  			  }
  		  }
  		  while_timeout = DWT->CYCCNT;
  		  ENCA_S = DWT->CYCCNT;
  		  while(HAL_GPIO_ReadPin(ENC3A_GPIO_Port, ENC3A_Pin) == 1){ // ootab kuni läheb madalaks
  			  if((DWT->CYCCNT - while_timeout)/2000 > 249){
  				  timeout_flag = 1;
  				  break;
  			  }
  		  }

		  ENCA_D = ((DWT->CYCCNT - ENCA_S) / 2000);
		  if(ENCA_D > 249 || timeout_flag == 1) ENCA_D = 249;
		  ENCA_P2 = (uint8_t)ENCA_D;






		if(received.speed1 > 125){
			uint8_t pi1d = PID2(ENCA_P3, (received.speed1 - 125)*2);
			Set_Motor_Speed(&(TIM4->CCR1), &(TIM4->CCR2), pi1d);
		}
		else if(received.speed1 < 125){
			uint8_t pi1d = PID2(ENCA_P3, 250 - (received.speed1*2));
			Set_Motor_Speed(&(TIM4->CCR1), &(TIM4->CCR2), pi1d*-1);
		}
		else{
			Set_Motor_Speed(&(TIM4->CCR1), &(TIM4->CCR2), 0);
		}



		if(received.speed2 > 125){
			uint8_t pi2d = PID2(ENCA_P, (received.speed2 - 125)*2);
			Set_Motor_Speed(&(TIM1->CCR1), &(TIM1->CCR2), pi2d);
		}
		else if(received.speed2 < 125){
			uint8_t pi2d = PID2(ENCA_P, 250 - (received.speed2*2));
			Set_Motor_Speed(&(TIM1->CCR1), &(TIM1->CCR2), pi2d*-1);
		}
		else{
			Set_Motor_Speed(&(TIM1->CCR1), &(TIM1->CCR2), 0);
		}





		if(received.speed3 > 125){
			uint8_t pi3d = PID2(ENCA_P2, (received.speed3 - 125)*2);
			Set_Motor_Speed(&(TIM3->CCR1), &(TIM3->CCR2), pi3d);
		}
		else if(received.speed3 < 125){
			uint8_t pi3d = PID2(ENCA_P2, 250 - (received.speed3*2));
			Set_Motor_Speed(&(TIM3->CCR1), &(TIM3->CCR2), pi3d*-1);
		}
		else{
			Set_Motor_Speed(&(TIM3->CCR1), &(TIM3->CCR2), 0);
		}






	    //CDC_Transmit_FS(&ENCA_P, sizeof(ENCA_P));



	//	uint8_t pi3d = PID2(ENCA_P3, received.speed3);
	//  CDC_Transmit_FS(&pid, sizeof(pid));
	// 	Set_Motor_Speed(&(TIM4->CCR1), &(TIM4->CCR2), pi3d);


    /* USER CODE END WHILE */

    /* USER CODE BEGIN 3 */
  }
  /* USER CODE END 3 */
}

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
/* USER CODE BEGIN 4 */
void HAL_TIM_PeriodElapsedCallback(TIM_HandleTypeDef *htim) {
//	unsigned long t1 = DWT->CYCCNT;

	//Handle_Encoder(&motor1, TIM2->CNT);
	//Handle_Encoder(&motor2, TIM2->CNT);

	//Handle_Encoder(&motor3, TIM4->CNT);
	if (command.pid_type == 0) {
	//	feedback.motor1 = motor1.cur_enc_speed;
		//received.speed2 = motor2.cur_enc_speed;

		//feedback.motor3 = motor3.cur_enc_speed;
	} else {
	//	feedback.motor1 = motor1.enc_speed_hist_avg;
		//received.speed2 = motor2.enc_speed_hist_avg;
	//	feedback.motor3 = motor3.enc_speed_hist_avg;
	}

	//Calculate_PID(&motor1);
//	Calculate_PID(&motor2);
	//Calculate_PID(&motor3);
	//Set_Motor_Speed(&(TIM1->CCR1), &(TIM1->CCR2), motor1.cur_speed);//motor1.cur_speed
	//Set_Motor_Speed(&(TIM3->CCR1), &(TIM3->CCR2), motor2.cur_speed);
	//Set_Motor_Speed(&(TIM4->CCR1), &(TIM4->CCR2), motor3.cur_speed);

	// servo stopper
//	if (HAL_GPIO_ReadPin(GPIOB, GPIO_PIN_3) && !command.ir) {
//		TIM17->CCR1 = 0;
//s	}

	// timeout
	if (command_received_ticker > 0) {
		command_received_ticker -= 1;
	} else {
		// stop wheels
		TIM1->CCR1 = 0;
		TIM1->CCR2 = 0;
		TIM3->CCR1 = 0;
		TIM3->CCR2 = 0;
		TIM4->CCR1 = 0;
		TIM4->CCR2 = 0;


	}
//	unsigned long t2 = DWT->CYCCNT;
//	unsigned long diff = t2 - t1;
}

/* USER CODE END 4 */
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


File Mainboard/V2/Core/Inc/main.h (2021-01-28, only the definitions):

#define MOTORS_MIN_CCR 20000
#define MOTORS_MAX_CCR 65000
#define MOTORS_MAX_SPEED 100
#define MOTORS_CO ((MOTORS_MAX_CCR - MOTORS_MIN_CCR) / MOTORS_MAX_SPEED)
#define ESC_IDLE_CCR 4000
#define ESC_MIN_CCR 4200
#define ESC_MAX_CCR 7000
#define ESC_MAX_SPEED 100
#define ESC_CO ((ESC_MAX_CCR - ESC_MIN_CCR) / ESC_MAX_SPEED)
#define SERVO_IN_MIN_CCR 4700
#define SERVO_OUT_MIN_CCR 5000
#define SERVO_MAX_SPEED 100
#define SERVO_CO (400/SERVO_MAX_SPEED)
#define ENCODER_MAX 65535
#define ENCODER_QUADRANT (ENCODER_MAX / 4)
#define ENCODER_QUADRANT_3 (ENCODER_QUADRANT * 3)
#define ENC3A_Pin GPIO_PIN_1
#define ENC3A_GPIO_Port GPIOF
#define ENC2_A_Pin GPIO_PIN_0
#define ENC2_A_GPIO_Port GPIOA
#define ENC1A_Pin GPIO_PIN_2
#define ENC1A_GPIO_Port GPIOA
#define ENC1B_Pin GPIO_PIN_3
#define ENC1B_GPIO_Port GPIOA
#define ENC1B_EXTI_IRQn EXTI3_IRQn
#define ENC3B_Pin GPIO_PIN_4
#define ENC3B_GPIO_Port GPIOA
#define ENC3B_EXTI_IRQn EXTI4_IRQn
#define ESCPWM_Pin GPIO_PIN_5
#define ESCPWM_GPIO_Port GPIOA
#define M1_PWM1_Pin GPIO_PIN_6
#define M1_PWM1_GPIO_Port GPIOA
#define M1_PWM2_Pin GPIO_PIN_7
#define M1_PWM2_GPIO_Port GPIOA
#define M2_PWM1_Pin GPIO_PIN_8
#define M2_PWM1_GPIO_Port GPIOA
#define M2_PWM2_Pin GPIO_PIN_9
#define M2_PWM2_GPIO_Port GPIOA
#define SERVOPWM_Pin GPIO_PIN_15
#define SERVOPWM_GPIO_Port GPIOA
#define M3_PWM1_Pin GPIO_PIN_6
#define M3_PWM1_GPIO_Port GPIOB
#define M3_PWM2_Pin GPIO_PIN_7
#define M3_PWM2_GPIO_Port GPIOB

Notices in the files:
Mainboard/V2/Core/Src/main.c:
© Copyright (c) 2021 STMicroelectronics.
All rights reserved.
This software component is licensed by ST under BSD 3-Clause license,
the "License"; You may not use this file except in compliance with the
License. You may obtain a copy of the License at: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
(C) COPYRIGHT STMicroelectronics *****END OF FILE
